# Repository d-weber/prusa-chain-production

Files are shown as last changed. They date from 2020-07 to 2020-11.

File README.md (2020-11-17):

# Prusa i3 MK3 Chain Production add-on
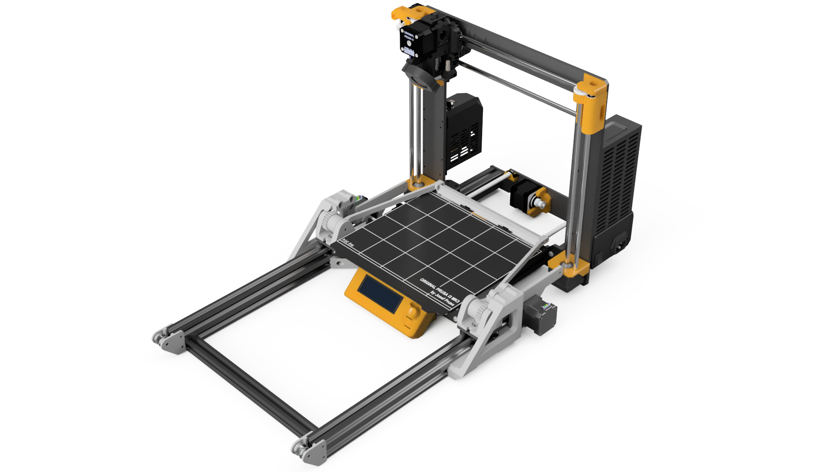
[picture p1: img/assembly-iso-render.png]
assembly iso render [assembly iso render

Add chain production capability to your Prusa i3

# How it works
- The arduino controls the steppers & fans
- The printer is controlled via octopi
- A [script](octoprint-plugin/main.py) on the octopi monitors the octoprint status and controls the arduino via usb-serial to start cooling and trigger the ejection

# Demo video
YT (https://www.youtube.com/watch?v=xZeJeUdq0wY)

# Assembly Bill of materials
Most of the parts can be ordered on Aliexpress at a small cost, for a total of approx $100

Description | Count | Français | English
------------ | ------------- | ------------- | -------------
Nema 17 stepper | 2 | [AliExpress](https://fr.aliexpress.com/item/32572890101.html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,searchweb201602_,searchweb201603_) | [AliExpress](https://www.aliexpress.com/item/32572890101.html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,searchweb201602_,searchweb201603_)
350mm 2040 V-SLOT Aluminium profile | 2 | [AliExpress](https://fr.aliexpress.com/item/32920516912.html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,searchweb201602_,searchweb201603_) | [AliExpress](https://www.aliexpress.com/item/32920516912.html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,searchweb201602_,searchweb201603_)
300mm 2020 V-SLOT Aluminium profile | 1 | [AliExpress](https://fr.aliexpress.com/item/32998701000.html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,searchweb201602_,searchweb201603_) | [AliExpress](https://www.aliexpress.com/item/32998701000.html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,searchweb201602_,searchweb201603_)
Mini V-SLOT gantry | 2 | [AliExpress](https://fr.aliexpress.com/item/32984815098.html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,searchweb201602_,searchweb201603_) | [AliExpress](https://www.aliexpress.com/item/32984815098.html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,searchweb201602_,searchweb201603_)
Angle bracket for 2020 | 2 | [AliExpress](https://fr.aliexpress.com/item/4001050647146.html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,searchweb201602_,searchweb201603_) | [AliExpress](https://www.aliexpress.com/item/4001050647146.html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,searchweb201602_,searchweb201603_)
20T 6MM GT2 Idler pulley | 2 | [AliExpress](https://fr.aliexpress.com/item/32822906447.html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,searchweb201602_,searchweb201603_) | [AliExpress](https://www.aliexpress.com/item/32822906447.html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,searchweb201602_,searchweb201603_)
20T 6MM GT2 Motor pulley | 2 | [AliExpress](https://fr.aliexpress.com/item/4000640547601.html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,searchweb201602_,searchweb201603_) | [AliExpress](https://www.aliexpress.com/item/4000640547601.html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,searchweb201602_,searchweb201603_)
1M 6MM GT2 Belt | 2 | [AliExpress](https://fr.aliexpress.com/item/32853559638.html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,searchweb201602_,searchweb201603_) | [AliExpress](https://www.aliexpress.com/item/32853559638.html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,searchweb201602_,searchweb201603_)
120MM 12V FAN | 2 | [AliExpress](https://fr.aliexpress.com/item/33000978834.html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,searchweb201602_,searchweb201603_) | [AliExpress](https://www.aliexpress.com/item/33000978834.html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,searchweb201602_,searchweb201603_)
TMC2130 SPI StepStick | 2 | [AliExpress](https://fr.aliexpress.com/item/32970150483.html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,searchweb201602_,searchweb201603_) | [AliExpress](https://www.aliexpress.com/item/32970150483.html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,searchweb201602_,searchweb201603_)
Arduino pro micro clone | 2 | [AliExpress](https://fr.aliexpress.com/item/32902569443.html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,searchweb201602_,searchweb201603_) | [AliExpress](https://www.aliexpress.com/item/32902569443.html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,searchweb201602_,searchweb201603_)
M4x10 HEX Screw | 50 | [AliExpress](https://fr.aliexpress.com/item/10000150053486.html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,searchweb201602_,searchweb201603_) | [AliExpress](https://www.aliexpress.com/item/10000150053486.html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,searchweb201602_,searchweb201603_)
M5x30 HEX Screw | 2 | [AliExpress](https://fr.aliexpress.com/item/10000150053486.html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,searchweb201602_,searchweb201603_) | [AliExpress](https://www.aliexpress.com/item/10000150053486.html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,searchweb201602_,searchweb201603_)
M5x50 HEX Screw | 2 | [AliExpress](https://fr.aliexpress.com/item/10000150053486.html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,searchweb201602_,searchweb201603_) | [AliExpress](https://www.aliexpress.com/item/10000150053486.html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,searchweb201602_,searchweb201603_)
M4x30 HEX Screw | 4 | [AliExpress](https://fr.aliexpress.com/item/10000150053486.html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,searchweb201602_,searchweb201603_) | [AliExpress](https://www.aliexpress.com/item/10000150053486.html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,searchweb201602_,searchweb201603_)
M4 NyLock Nut | 4 | [AliExpress](https://fr.aliexpress.com/item/32988995881.html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,searchweb201602_,searchweb201603_) | [AliExpress](https://www.aliexpress.com/item/32988995881.html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,searchweb201602_,searchweb201603_)
M4 2020 Nut | 50 | [AliExpress](https://fr.aliexpress.com/item/33043957747.html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,searchweb201602_,searchweb201603_) | [AliExpress](https://www.aliexpress.com/item/33043957747.html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,searchweb201602_,searchweb201603_)
M4 3030 Nut | 4 | [AliExpress](https://fr.aliexpress.com/item/33043957747.html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,searchweb201602_,searchweb201603_) | [AliExpress](https://www.aliexpress.com/item/33043957747.html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,searchweb201602_,searchweb201603_)

# Ejector PCB
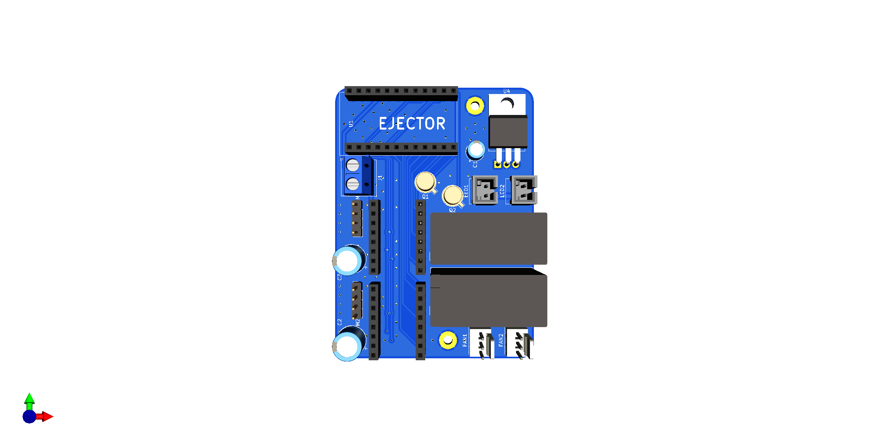
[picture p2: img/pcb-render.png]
assembly iso render [assembly iso render

Can be ordered through jlcpcb or any similar service

# Electronics Bill of materials
Description | Count | Français | English
------------ | ------------- | -------------
TMC2130 SPI StepStick | 2 | [AliExpress](https://fr.aliexpress.com/item/32970150483.html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,searchweb201602_,searchweb201603_) | [AliExpress](https://www.aliexpress.com/item/32970150483.html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,searchweb201602_,searchweb201603_)
Arduino pro micro clone | 2 | [AliExpress](https://fr.aliexpress.com/item/32902569443.html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,searchweb201602_,searchweb201603_) | [AliExpress](https://www.aliexpress.com/item/32902569443.html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,searchweb201602_,searchweb201603_)

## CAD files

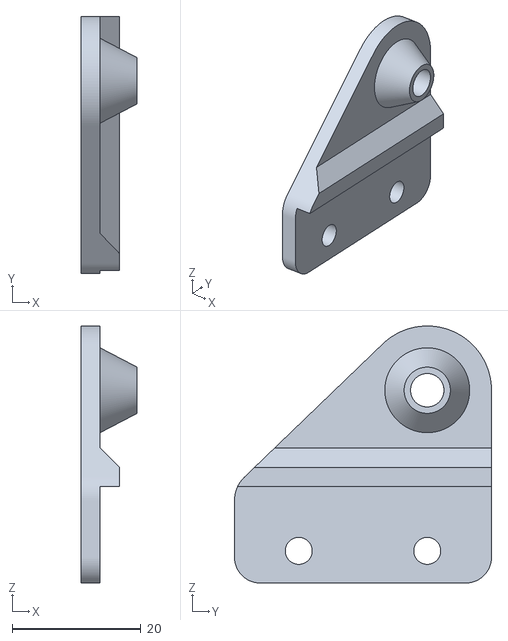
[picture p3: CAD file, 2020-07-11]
ejector-parts/stl/pulley_left.stl
8.75 x 40.0 x 40.0

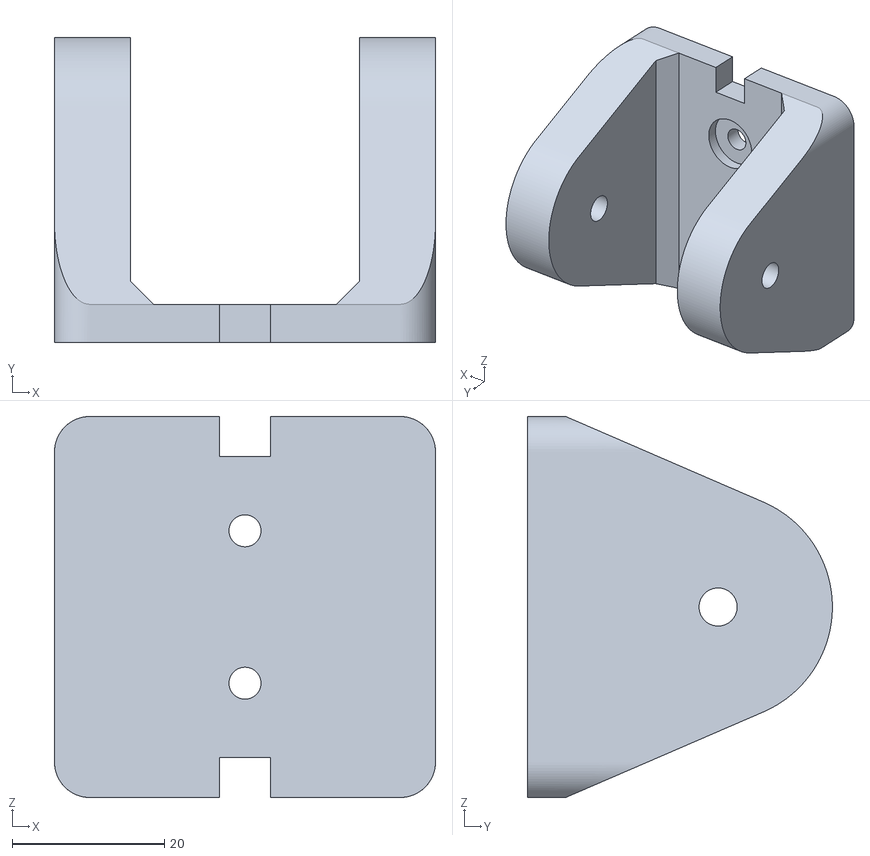
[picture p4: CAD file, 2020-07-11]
ejector-parts/stl/gear_support.stl
50.0 x 40.0 x 50.0

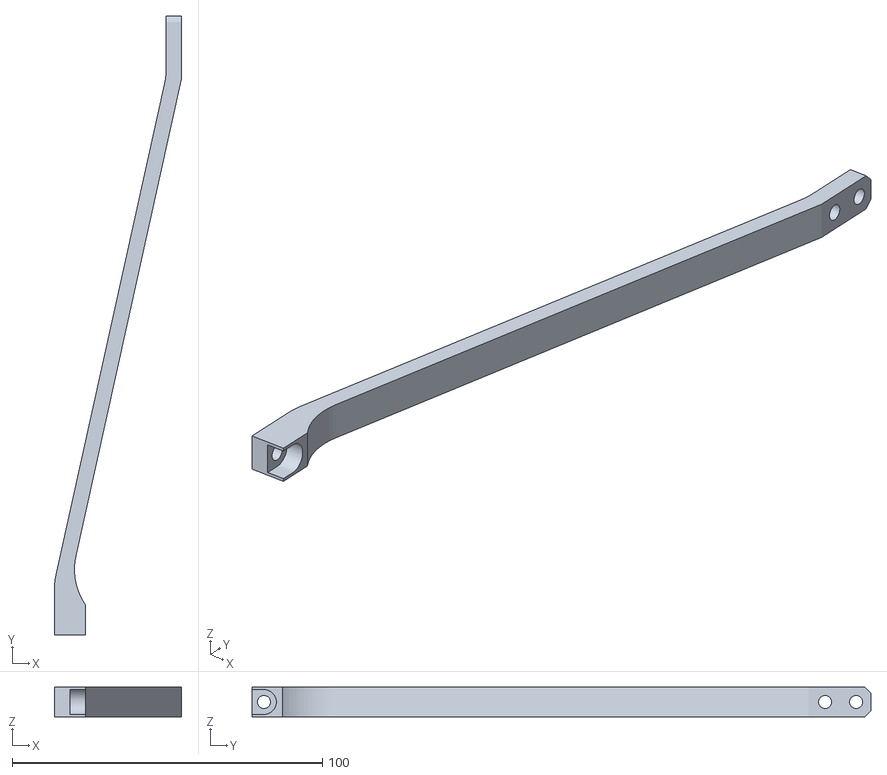
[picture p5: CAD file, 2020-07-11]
ejector-parts/stl/scrapper_arm_left.stl
41.0 x 199.6 x 9.60

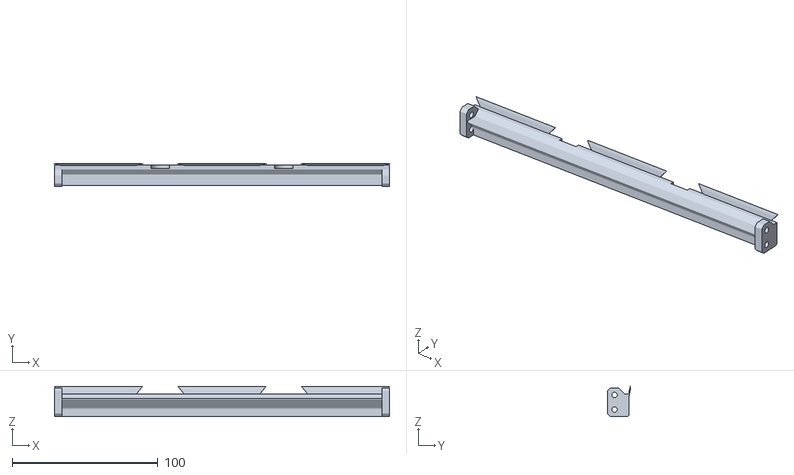
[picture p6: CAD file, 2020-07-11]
ejector-parts/stl/scrapper.stl
230.1 x 15.7 x 20.6

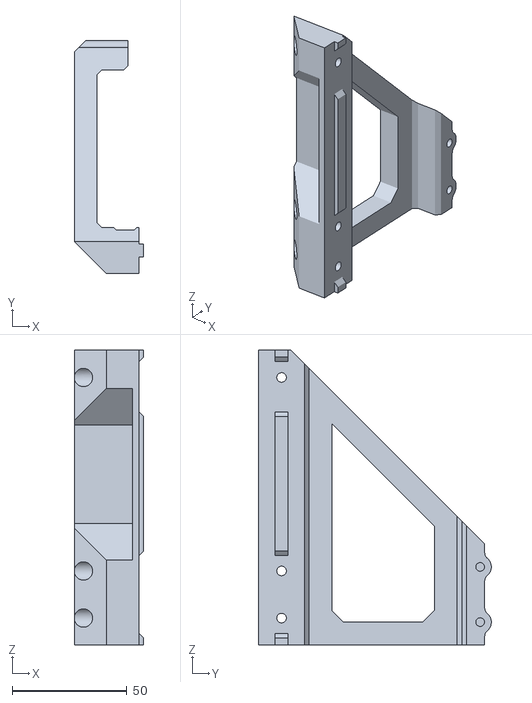
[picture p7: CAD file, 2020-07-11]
ejector-parts/stl/rack_support_left.stl
30.3 x 101.6 x 128.8

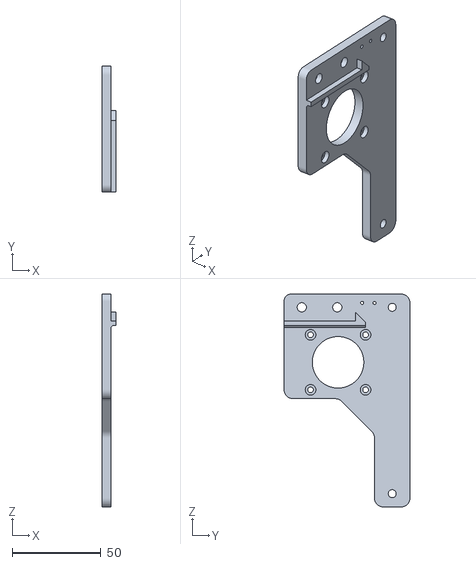
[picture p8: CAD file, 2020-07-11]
ejector-parts/stl/motor_mount_left.stl
8.00 x 70.9 x 120.0

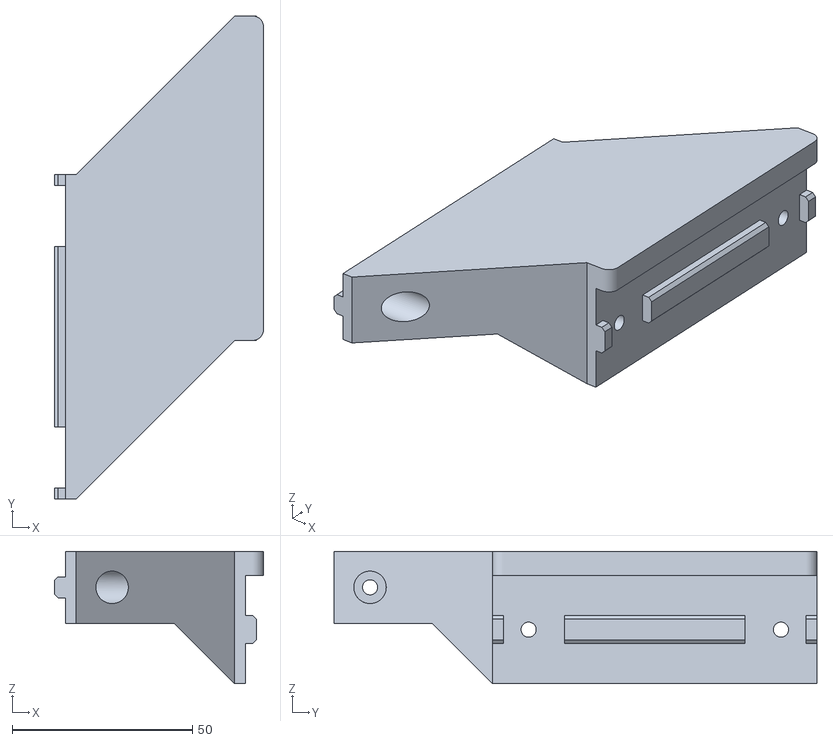
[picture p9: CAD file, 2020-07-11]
ejector-parts/stl/link_right.stl
58.0 x 134.0 x 36.8

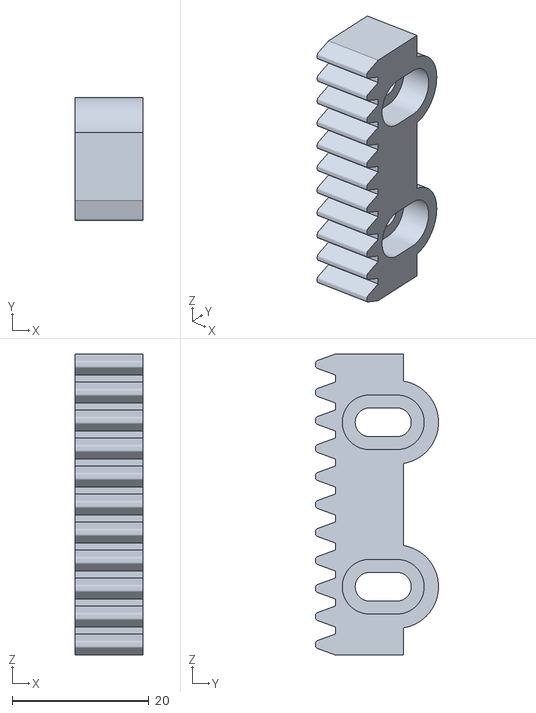
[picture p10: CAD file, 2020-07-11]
ejector-parts/stl/gear_rack.stl
10.00 x 18.0 x 44.1

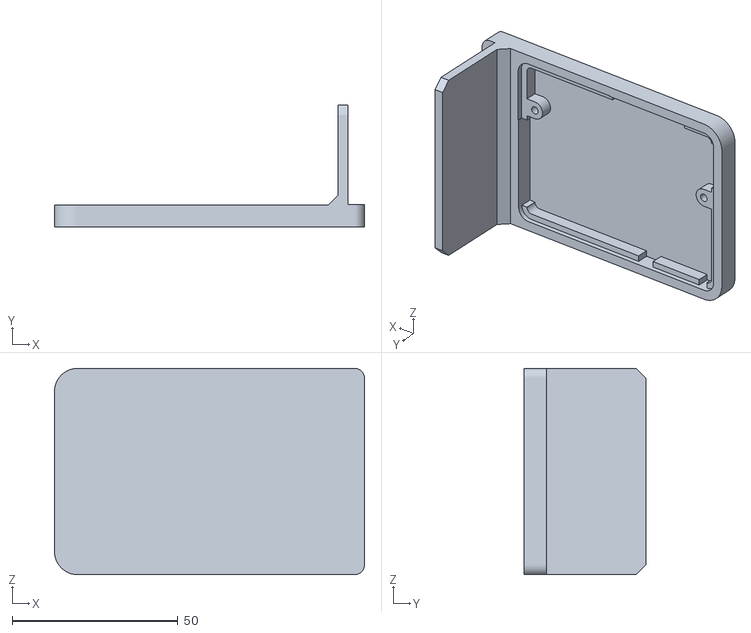
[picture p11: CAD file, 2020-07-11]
ejector-parts/stl/pcb_holder.stl
93.5 x 36.7 x 62.3

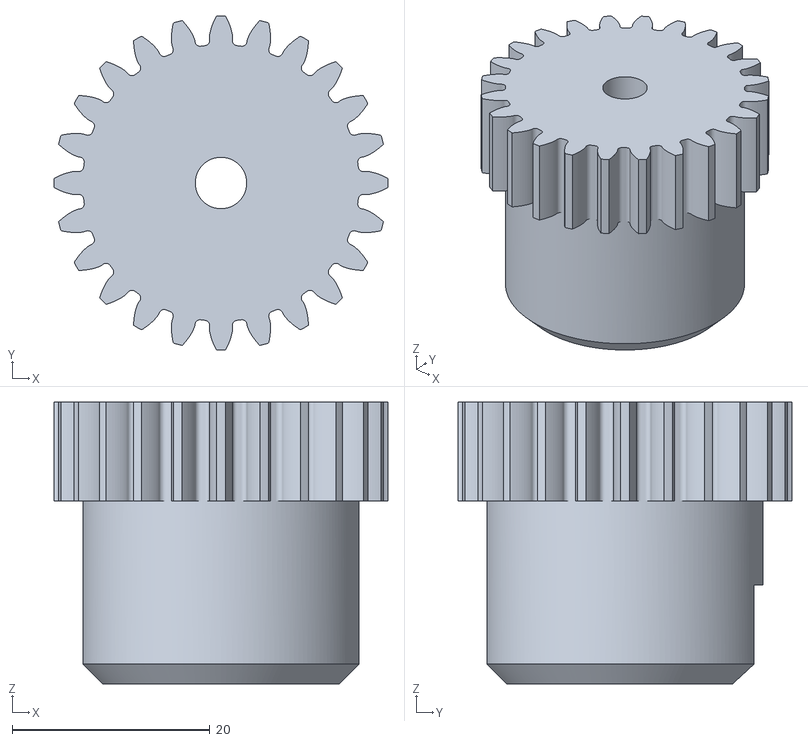
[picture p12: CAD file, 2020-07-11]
ejector-parts/stl/gear.stl
33.8 x 33.8 x 28.5

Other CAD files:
ejector-parts/stl/rack_support_right.stl
ejector-parts/stl/link_left.stl
ejector-parts/stl/scrapper_arm_right.stl
ejector-parts/stl/motor_mount_right.stl
ejector-parts/stl/pulley_right.stl

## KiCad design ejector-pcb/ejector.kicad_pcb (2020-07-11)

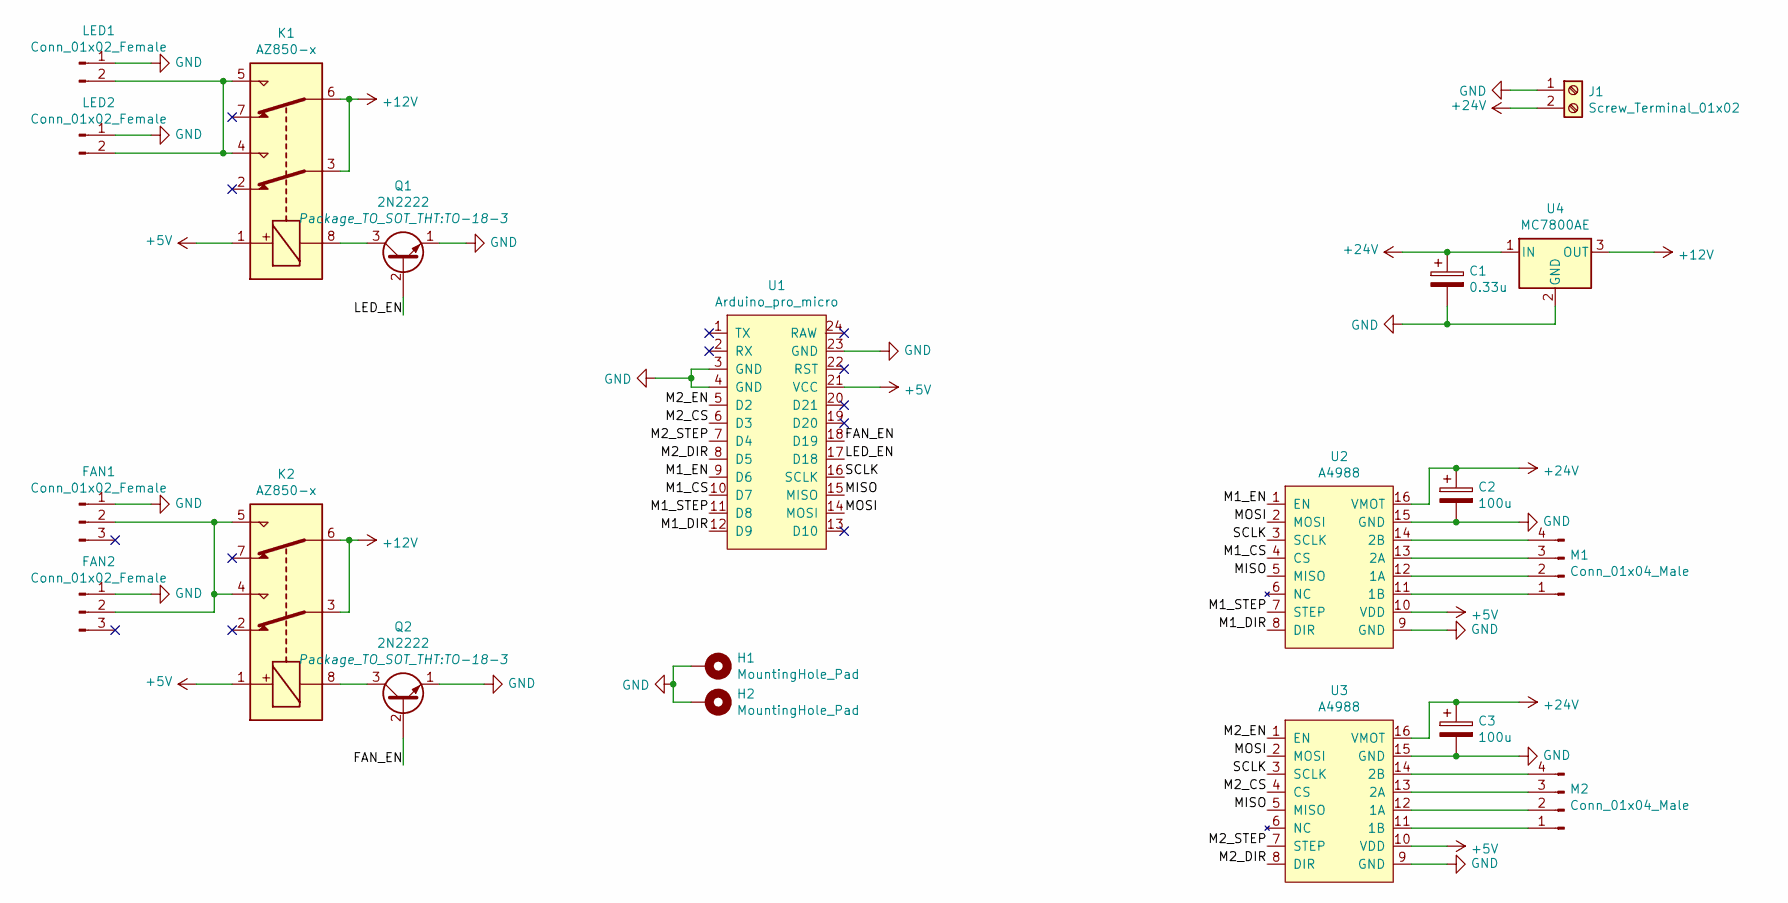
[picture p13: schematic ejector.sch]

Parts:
C1: 0.33u; CP_Radial_D5.0mm_P2.00mm
C2, C3: 100u; CP_Radial_D8.0mm_P3.50mm
FAN1, FAN2: Conn_01x02_Female; Molex_KK-254_AE-6410-03A_1x03_P2.54mm_Vertical
H1, H2: MountingHole_Pad; MountingHole_2.5mm_Pad
J1: Screw_Terminal_01x02; TerminalBlock_Phoenix_MKDS-1,5-2-5.08_1x02_P5.08mm_Horizont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
K1, K2: AZ850-x; Relay_DPDT_Panasonic_JW2
LED1, LED2: Conn_01x02_Female; Molex_SL_171971-0002_1x02_P2.54mm_Vertical
M1, M2: Conn_01x04_Male; PinHeader_1x04_P2.54mm_Vertical
Q1, Q2: 2N2222; TO-18-3
U1: Arduino_pro_micro; ARDUINOPROMICRO
U2, U3: A4988
U4: MC7800AE; TO-220-3_Horizontal_TabDown

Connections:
+5V: K1.1, K2.1, U1.21 (VCC), U2.10 (VDD), U3.10 (VDD)
+12V: K1.3, K1.6, K2.3, K2.6, U4.3 (OUT)
+24V: C1.1, C2.1, C3.1, J1.2, U2.16 (VMOT), U3.16 (VMOT), U4.1 (IN)
/FAN_EN: Q2.2 (B), U1.18 (D19)
/LED_EN: Q1.2 (B), U1.17 (D18)
/M1_CS: U1.10 (D7), U2.4 (CS)
/M1_DIR: U1.12 (D9), U2.8 (DIR)
/M1_EN: U1.9 (D6), U2.1 (EN)
/M1_STEP: U1.11 (D8), U2.7 (STEP)
/M2_CS: U1.6 (D3), U3.4 (CS)
/M2_DIR: U1.8 (D5), U3.8 (DIR)
/M2_EN: U1.5 (D2), U3.1 (EN)
/M2_STEP: U1.7 (D4), U3.7 (STEP)
/MISO: U1.15 (MISO), U2.5 (MISO), U3.5 (MISO)
/MOSI: U1.14 (MOSI), U2.2 (MOSI), U3.2 (MOSI)
/SCLK: U1.16 (SCLK), U2.3 (SCLK), U3.3 (SCLK)
GND: C1.2, C2.2, C3.2, FAN1.1, FAN2.1, H1.1, H2.1, J1.1, LED1.1, LED2.1, Q1.1 (E), Q2.1 (E), U1.3 (GND), U1.4 (GND), U1.23 (GND), U2.9 (GND), U2.15 (GND), U3.9 (GND), U3.15 (GND), U4.2 (GND)
unnamed: FAN1.2, FAN2.2, K2.4, K2.5
unnamed: K1.4, K1.5, LED1.2, LED2.2
unnamed: K1.8, Q1.3 (C)
unnamed: K2.8, Q2.3 (C)
unnamed: M1.1, U2.11 (1B)
unnamed: M1.2, U2.12 (1A)
unnamed: M1.3, U2.13 (2A)
unnamed: M1.4, U2.14 (2B)
unnamed: M2.1, U3.11 (1B)
unnamed: M2.2, U3.12 (1A)
unnamed: M2.3, U3.13 (2A)
unnamed: M2.4, U3.14 (2B)

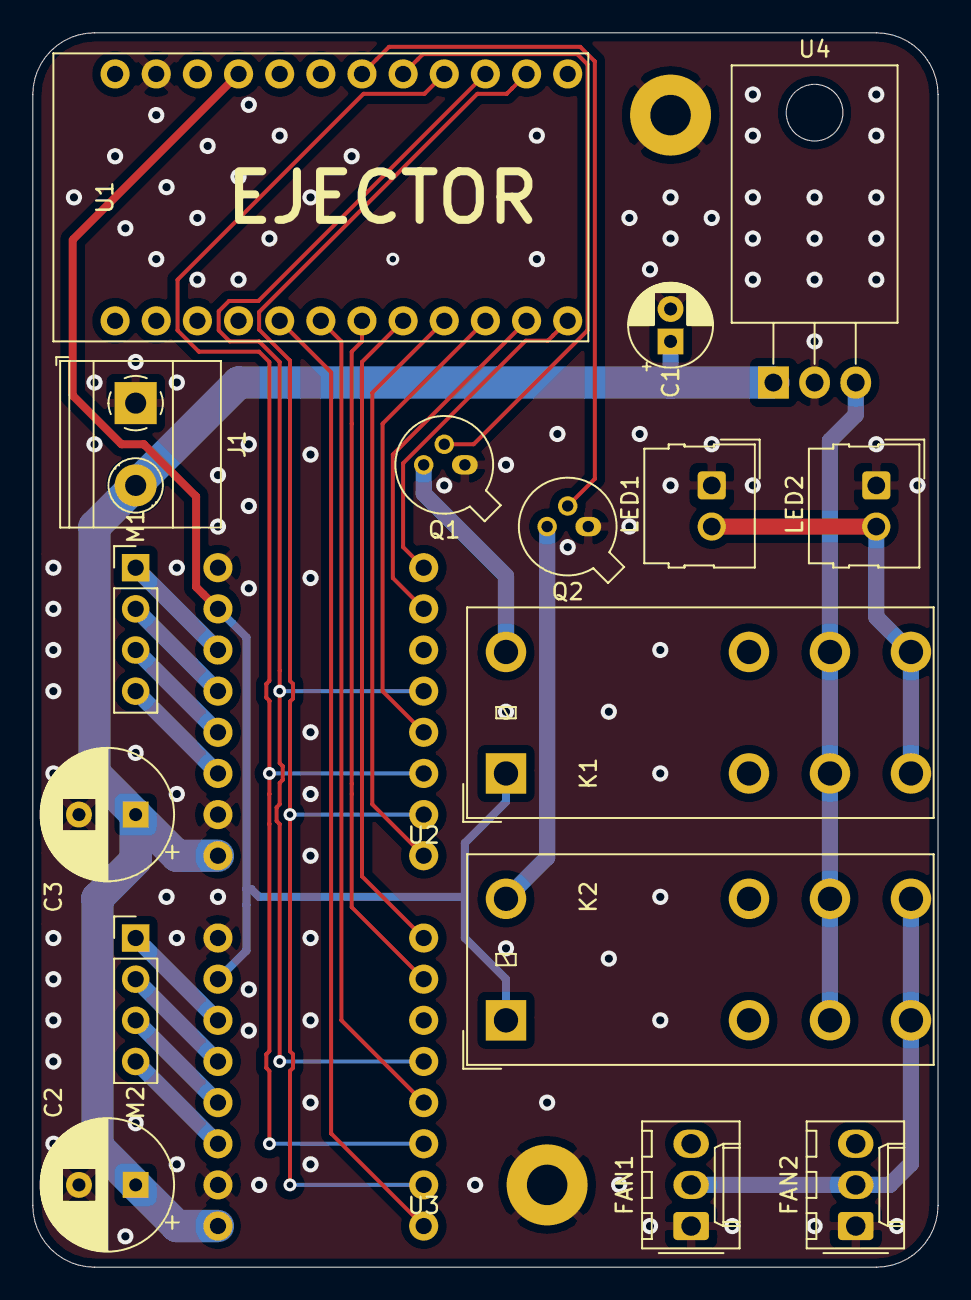
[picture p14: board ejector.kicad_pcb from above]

Board: 2 copper layers, 55.9 x 76.2 mm, 20 parts (0 on the bottom side), 29 nets.

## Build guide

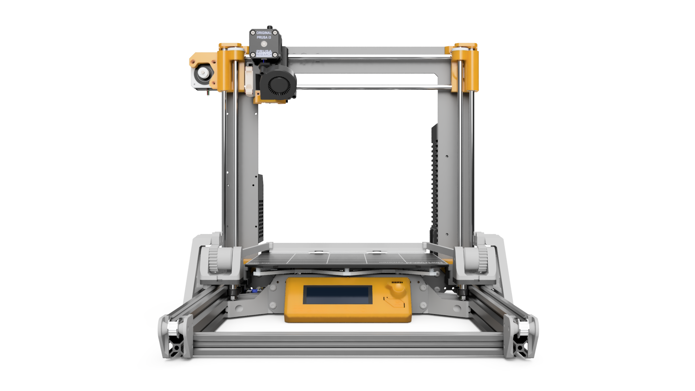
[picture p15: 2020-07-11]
img/assembly-front-render.png

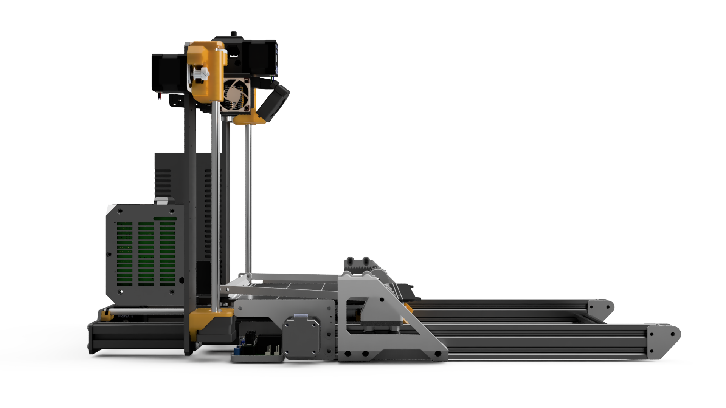
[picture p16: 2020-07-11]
img/assembly-left-render.png

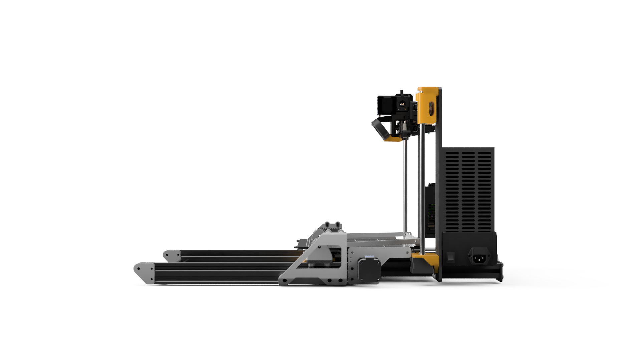
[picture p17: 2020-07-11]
img/assembly-right-render.png

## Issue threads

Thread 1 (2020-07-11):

Needs an octoprint plugin

d-weber, 2020-07-11:
We should be able to control the ejector via octoprint & also queue prints.

d-weber, 2020-07-11:
The plugin may allow to:
- Select & Save the arduino port (same as for the printer)
- Manually trigger Ejector procedure
- Manually trigger FAN OFF/ON
- Manually trigger LED OFF/ON
- Set the cooling time after a print is finished (15min for me)
- Queue gcodes & number of prints per gcode

Arduino baudrate : 9600
All commands must end with `\n`

Arduino commands:
Description | Command | Response
----- | ----- | -----
Connection test | PING | PONG
Homing | HOME | START & END
Extend ejector | END | START & END
Ejection procedure) | EJECT | START & END
Turn on fans | FAN ON | DONE
Turn off fans | FAN OFF | DONE
Turn on leds | LED ON | DONE
Turn on leds | LED OFF | DONE

mmiscool, 2020-07-11:
Hello,
I am with Autodrop3d and would love to talk with you about the possibility of connecting to our cloud print platform that has queing and was specifically designed for printers with automatic part ejection. We have a gcode sender client that runs on a raspberry pi written in python. I think it would be a matter of a few hours to make a plug-in that handles your unique ejector and I would be happy to hop on a call to make that happen.

A little background on Autodrop3d. It has queing, routing to machine based on print size, location and material. It also supports monitization in shared private or public environments. The platform also included built in browser based parametric modeling allowing for a completely web based 3d printer workflow.

If you are interested we can set up a Google Hangouts meet and make it happen.

d-weber, 2020-07-21:
Thanks @mmiscool , i think you have all the data in this repo to make a plugin for you interface, you can simply plug the arduino on your raspberry ;).

However we're discussing about an octoprint plugin here :)

Faceless3D, 2020-11-21:
Hi,

i´m having troubles getting the octoprint plugin to work. Do i have to modify the main.py and insert the API and IP Adress of the Pi? Do i use the global API or a application API Key ? Is port 80 always correct? Under /dev i can see ttyACM0 but not ttyACM1 which one is correct? I´m using a Raspberry Pi Zero. Do i "install" the Plugin via the Plugin Manager in Octoprint?

Sorry for so many question. It´s the last step of getting this system to work.

Thank you

Faceless3D, 2020-11-25:
Hi,

how do you queue or loop printjobs right now? Is there an elegant way of doing it?
I use the plugin "continuous print" with a wait time between jobs (G4 Pxxx). The wait time is the cooling time + ejection duration. While waiting between jobs the printer status is "finishing", i had to replace "operational" with "finishing"  in the plugin.

So this method of bed cleaing works perfect with PETG and the textured PEI bed. Now i have to build 10 more for the whole farm.

Thank you

Marwitch, 2021-06-08:
Hello,
the octoprint plugin does not work for me.
Is it possible to make an update please?
-----------------------------------------------------------------------
Incompatible to OctoPrint or the underlying Python environment
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

Marwitch, 2021-06-08:
Hello!
so what about the plugin?

Marwitch, 2021-06-09:
Hello @d-weber,
unfortunately the plugin is no longer functional.
Please update :)

modtoy95, 2021-09-14:
how can i get this working on octo print?

Marwitch, 2021-09-14:
Hi, I made my own motor control and my own code for arduino :) I use the "continuous print" plugin in octoprint. Everything works the same just I don't have communication between the printer and raspberry ..

modtoy95, 2021-09-15:
would you be willing to share how you did i?

modtoy95, 2021-09-15:
it?

bastian123321, 2022-06-02:
It seems that the plugin isnt working anymore on new Octoprint versions, was the plugin written in python 2 or 3?

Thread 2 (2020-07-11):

Update the arduino code for TMC2130 support

d-weber, 2020-07-11:
The arduino code is actually made for A4988 drivers & 4 microswitch endstops

It should use TMC2130 stallguard function to detect endstops & detect ejection fails to retry

Faceless3D, 2020-11-07:
Hi,

thank you for this great project! I just finished the PCB and want to test the system. Do you know when the code for the TMC2130 Stepper is available? Unfortunetly i can´t code :(

Thank you

Faceless3D, 2020-11-07:
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

d-weber, 2020-11-17:
Great ! i'll update the code tonight

d-weber, 2020-11-17:
Done, you mayd need to tune STALL_VALUE @Faceless3D

Faceless3D, 2020-11-21:
Thank you!

STALL_VALUE 9 works good for me. I also increased the acceleration a bit.

d-weber, 2020-12-18:
Implemented in #9

bnykolass, 2022-06-03:
Please, where should I put the script in octoprint?
It doesn't work for me as a plugin.
Well thank you

Closed 2020-12-18.

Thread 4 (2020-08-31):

Pulley bores missing

tim-lukacik, 2020-08-31:
I believe the bill of materials is missing one specification for
20T 6MM GT2 Idler pulley
20T 6MM GT2 Motor pulley

I assume "B5" idler, "inner hole 5mm" motor as these are riding on the m5 screws?

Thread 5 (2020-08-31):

PCB ordering guide

tim-lukacik, 2020-08-31:
When trying to order the PCB I am able to upload the gerber.zip file successfully but how do I provide the SMT components for assembly? JLCPCB seems to be looking for BOM or CPL files. Sorry if I am missing something I have not ordered custom PCBs before.

I can make a PR with a guide for others once I understand the whole process.

Baelt, 2021-02-02:
hello there
I would also be very interested in how to buy/order the PCB...
Greetings Ulrich

modtoy95, 2021-08-24:
Did you figure out how to add or generate a BOM file?

Marwitch, 2021-09-14:
I had the PCB made and used all the components, unfortunately after measuring I found out that the PCB is badly made and I threw it away! I made my own code for arduino and I control it via the endstop switch :D

modtoy95, 2021-09-14:
Thats exactly what I was thinking of doing. With an end stop switch. I even looked around on fiver to see if some on could code something similar. Would it be to much to ask if you are willing to share or sell your idea to me? I've been trying to automated my printers for a while now. I even bought quinley automation, but I'm not a fan of the print head pushing the parts out. 

Sent from Yahoo Mail on Android

  On Tue, Sep 14, 2021 at 12:35 AM, ***@***.***> wrote:

I had the PCB made and used all the components, unfortunately after measuring I found out that the PCB is badly made and I threw it away! I made my own code for arduino and I control it via the endstop switch :D

—
You are receiving this because you commented.
Reply to this email directly, view it on GitHub, or unsubscribe.
Triage notifications on the go with GitHub Mobile for iOS or Android.

modtoy95, 2021-09-15:
I hired some one on fiver to rewrite the code to trigger with a switch, but nothing happens idk what's wrong. 

Sent from Yahoo Mail on Android

  On Tue, Sep 14, 2021 at 2:47 AM, Luis ***@***.***> wrote:   Thats exactly what I was thinking of doing. With an end stop switch. I even looked around on fiver to see if some on could code something similar. Would it be to much to ask if you are willing to share or sell your idea to me? I've been trying to automated my printers for a while now. I even bought quinley automation, but I'm not a fan of the print head pushing the parts out. 

Sent from Yahoo Mail on Android

  On Tue, Sep 14, 2021 at 12:35 AM, ***@***.***> wrote:

I had the PCB made and used all the components, unfortunately after measuring I found out that the PCB is badly made and I threw it away! I made my own code for arduino and I control it via the endstop switch :D

—
You are receiving this because you commented.
Reply to this email directly, view it on GitHub, or unsubscribe.
Triage notifications on the go with GitHub Mobile for iOS or Android.

KilianWS, 2021-11-16:
hello there
has someone found a way to create the BOM and CPL file for JLCPCB?
@tim-lukacik or did you find another way to order it?

tyneff, 2022-12-11:
Hi,

Also having trouble getting the PCB made with all components. Has anyone been able to do so successfully? Would happily purchase a built PCB

ant0nyk1ng, 2023-11-29:
> I hired some one on fiver to rewrite the code to trigger with a switch, but nothing happens idk what's wrong.  Sent from Yahoo Mail on Android On Tue, Sep 14, 2021 at 2:47 AM, Luis ***@***.***> wrote: Thats exactly what I was thinking of doing. With an end stop switch. I even looked around on fiver to see if some on could code something similar. Would it be to much to ask if you are willing to share or sell your idea to me? I've been trying to automated my printers for a while now. I even bought quinley automation, but I'm not a fan of the print head pushing the parts out.  Sent from Yahoo Mail on Android On Tue, Sep 14, 2021 at 12:35 AM, ***@***.***> wrote: I had the PCB made and used all the components, unfortunately after measuring I found out that the PCB is badly made and I threw it away! I made my own code for arduino and I control it via the endstop switch :D — You are receiving this because you commented. Reply to this email directly, view it on GitHub, or unsubscribe. Triage notifications on the go with GitHub Mobile for iOS or Android.

Did you get this to work? can I chat to you about what you did?

ant0nyk1ng, 2023-11-29:
> I had the PCB made and used all the components, unfortunately after measuring I found out that the PCB is badly made and I threw it away! I made my own code for arduino and I control it via the endstop switch :D

I see you have a fork but there is no information on the arduino code?

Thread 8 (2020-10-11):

Can this system work with a smooth pei sheet?

DoWhileGeek, 2020-10-11:
I can see how a textured bed works really well for this system, as most parts will pop themselves loose, especially given the cooling routine. But what about smooth pei? Most of my products need to be printed on a smooth sheet, and I was wondering if you've done any testing with it?

Marwitch, 2021-09-14:
Hi, I also print on a smooth surface and it's no problem. You just have to be careful to adjust the guide knife on the pad! It is better to adjust the whole part and not put sharp edges there, as this could damage the pad!

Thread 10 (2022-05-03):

How does this system communicate with the 3D printer?

JimmyRam, 2022-05-03:
Does this system get connected directly to a raspberry pi and get controlled through octo print or does it get connected to the main board some how. I'm a bit confused on how to wire everything together? I'm still pretty new to electronics so I might just be missing something obvious.

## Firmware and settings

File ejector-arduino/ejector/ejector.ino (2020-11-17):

#include <TMCStepper.h>
#include <AccelStepper.h>
#define R_SENSE 0.11f
using namespace TMC2130_n;

// Serial commands
#define CMD_UNKNOWN 0
#define CMD_PING    1
#define CMD_HOME    2
#define CMD_END     3
#define CMD_EJECT   4
#define CMD_FAN_ON  5
#define CMD_FAN_OFF 6
#define CMD_LED_ON  7
#define CMD_LED_OFF 8
#define CMD_MOVE_FRONT 9
#define CMD_MOVE_REAR 10

// Motor 1
#define PIN_M1_ENABLE 6
#define PIN_M1_CS 7
#define PIN_M1_STEP 8
#define PIN_M1_DIR 9
TMC2130Stepper driverM1(PIN_M1_CS, R_SENSE);
AccelStepper stepperM1 = AccelStepper(AccelStepper::DRIVER, PIN_M1_STEP, PIN_M1_DIR);

// Motor 2
#define PIN_M2_ENABLE 2
#define PIN_M2_CS 3
#define PIN_M2_STEP 4
#define PIN_M2_DIR 5
TMC2130Stepper driverM2(PIN_M2_CS, R_SENSE);
AccelStepper stepperM2 = AccelStepper(AccelStepper::DRIVER, PIN_M2_STEP, PIN_M2_DIR);

// Other pins
#define PIN_LED 18
#define PIN_FAN 19

// Config
#define MICROSTEP 4
#define MAX_MOVING_TIME 10 // s
#define DEBUG false 
#define STEPS_PER_MM 5
#define STALL_VALUE 6
#define MAX_STALL 100

int maxPos = 280;
long mm2Step(long distance) {
  return  distance * STEPS_PER_MM * MICROSTEP;
}

long step2mm(long step) {
  return step / STEPS_PER_MM / MICROSTEP;
}

void setup() {
  Serial.begin(115200);

  // Fan & leds relays
  pinMode(PIN_LED, OUTPUT);
  pinMode(PIN_FAN, OUTPUT);
  pinMode(PIN_M1_CS, OUTPUT);
  pinMode(PIN_M2_CS, OUTPUT);

  while (!Serial) {
    ; // wait for serial port to connect. Needed for native USB
  }

  // Test relays
  digitalWrite(PIN_FAN, HIGH); 
  delay(1000);
  digitalWrite(PIN_FAN, LOW); 
  delay(500);
  digitalWrite(PIN_LED, HIGH); 
  delay(1000);
  digitalWrite(PIN_LED, LOW);

  // Enable SPI
  SPI.begin();
  pinMode(MISO, INPUT_PULLUP);

  // Init M1
  driverM1.begin();
  driverM1.rms_current(1000);
  driverM1.toff(4);
  driverM1.blank_time(24);
  driverM1.microsteps(MICROSTEP);
  driverM1.TCOOLTHRS(0xFFFFF); // 20bit max
  driverM1.THIGH(0);
  driverM1.semin(5);
  driverM1.semax(2);
  driverM1.sedn(0b01);
  driverM1.sgt(STALL_VALUE);
  driverM1.switchCSpin(LOW);
  stepperM1.setMaxSpeed(100 * MICROSTEP);
  stepperM1.setAcceleration(1000 * MICROSTEP);
  stepperM1.setEnablePin(PIN_M1_ENABLE);
  stepperM1.setPinsInverted(false, false, true);
  stepperM1.disableOutputs();

  // Init M2
  driverM2.begin();
  driverM2.rms_current(1000);
  driverM2.toff(4);
  driverM2.blank_time(24);
  driverM2.microsteps(MICROSTEP);
  driverM2.TCOOLTHRS(0xFFFFF); // 20bit max
  driverM2.THIGH(0);
  driverM2.semin(5);
  driverM2.semax(2);
  driverM2.sedn(0b01);
  driverM2.sgt(STALL_VALUE);
  driverM2.switchCSpin(LOW);
  stepperM2.setMaxSpeed(100 * MICROSTEP);
  stepperM2.setAcceleration(1000 * MICROSTEP);
  stepperM2.setEnablePin(PIN_M2_ENABLE);
  stepperM2.setPinsInverted(false, false, true);
  stepperM2.disableOutputs();
}

int parseStringCommand(String stringCommand) {
    if (stringCommand.equals("PING")) {
      return CMD_PING;
    } else if (stringCommand.equals("MOVE FRONT")) {
      return CMD_MOVE_FRONT;
    } else if (stringCommand.equals("MOVE REAR")) {
      return CMD_MOVE_REAR;
    } else if (stringCommand.equals("HOME")) {
      return CMD_HOME;
    } else if (stringCommand.equals("END")) {
      return CMD_END;
    } else if (stringCommand.equals("EJECT")) {
      return CMD_EJECT;
    } else if (stringCommand.equals("FAN ON")) {
      return CMD_FAN_ON;
    } else if (stringCommand.equals("FAN OFF")) {
      return CMD_FAN_OFF;
    } else if (stringCommand.equals("LED ON")) {
      return CMD_LED_ON;
    } else if (stringCommand.equals("LED OFF")) {
      return CMD_LED_OFF;
    } else {
      return CMD_UNKNOWN  ;
    }
}

int getM1StallValue() {
  DRV_STATUS_t drv_status{0};
  drv_status.sr = driverM1.DRV_STATUS();
  return drv_status.sg_result;
}

int getM2StallValue() {
  DRV_STATUS_t drv_status{0};
  drv_status.sr = driverM2.DRV_STATUS();
  return drv_status.sg_result;
}

long moveTo(long distance, long speed, bool sync = true) {
  stepperM1.setMaxSpeed(speed * MICROSTEP);
  stepperM2.setMaxSpeed(speed * MICROSTEP);
  stepperM1.moveTo(mm2Step(distance));
  stepperM2.moveTo(mm2Step(distance));
  uint32_t startTime = millis();
  uint32_t lastTime = millis();
  uint32_t lastStallCheck = millis();
  while(true) {
    stepperM1.run();
    stepperM2.run();

    if ((millis() - lastStallCheck) > 10) {
      lastStallCheck = millis();
      int M1StallValue = getM1StallValue();
      int M2StallValue = getM2StallValue();

      if ((millis() - startTime) > 100 && (M1StallValue < MAX_STALL || M2StallValue < MAX_STALL)){
        if (M1StallValue < MAX_STALL) {
          if (DEBUG) Serial.print("Stalled M1: ");
          if (DEBUG) Serial.println(M1StallValue, DEC);
          stepperM1.move(0);
          stepperM1.setSpeed(0);
        }
        if (M2StallValue < MAX_STALL) {
          if (DEBUG) Serial.print("Stalled M2: ");
          if (DEBUG) Serial.println(M2StallValue, DEC);
          stepperM2.move(0);
          stepperM2.setSpeed(0);
        }
        if (sync) {
          stepperM1.move(0);
          stepperM2.move(0);
          stepperM1.setSpeed(0);
          stepperM2.setSpeed(0);
        }
        break;
      }
    }

    if (!stepperM1.isRunning() && !stepperM2.isRunning()){
      break;
    }
  }

  long avgPos = (stepperM1.currentPosition() + stepperM2.currentPosition()) / 2;
  return step2mm(avgPos);
}

void eject() {
  stepperM1.enableOutputs();
  stepperM2.enableOutputs();

  // Deploy arm
  int pos = moveTo(70, 100);
  int i = 0;
  int speeds[] = {600, 500, 400, 300, 200};

  while (pos < maxPos * 0.95) {
    stepperM1.move(0);
    stepperM2.move(0);
    stepperM1.setSpeed(0);
    stepperM2.setSpeed(0);

    delay(500);
    moveTo(70, 500);
    delay(500);

    pos = moveTo(maxPos, speeds[i]);
    i++;
    if (i > 4) {
      i = 0;
    }
  }
  while (pos > 75) {
    pos  = moveTo(70, 500);
  }
  while (pos > 5) {
    pos  = moveTo(0, 100);
  }
  
  stepperM1.disableOutputs();
  stepperM2.disableOutputs();
}

void loop() {
  if (Serial.available() > 0) {
    String stringCommand = Serial.readStringUntil('\n');
    int command = parseStringCommand(stringCommand);
    switch (command) {
      case CMD_PING:
        Serial.println("PONG");
        break;
      case CMD_END:
        Serial.println("START");
        Serial.println("END");
        break;
      case CMD_EJECT:
        Serial.println("START");
        eject();
        Serial.println("END");
        break;
      case CMD_FAN_ON:
        digitalWrite(PIN_FAN, HIGH); 
        Serial.println("DONE");
        break;
      case CMD_FAN_OFF:
        digitalWrite(PIN_FAN, LOW); 
        Serial.println("DONE");
        break;
      case CMD_LED_ON:
        digitalWrite(PIN_LED, HIGH); 
        Serial.println("DONE");
        break;
      case CMD_LED_OFF:
        digitalWrite(PIN_LED, LOW); 
        Serial.println("DONE");
        break;
      default:
      case CMD_UNKNOWN:
        Serial.println("UNKNOWN COMMAND");
    }
  }
}

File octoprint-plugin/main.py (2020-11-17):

import requests
import sys
import time
import datetime
import json
import serial

# Constants
OCTOPRINT_API_KEY = ''
OCTOPRINT_HOST = 'localhost'
OCTOPRINT_PORT = '80'
EJECTOR_TTY = '/dev/ttyACM1'
EJECTION_TEMP = 30
COOLING_TIME = 900 # 15Min
AUTO_RESTART = False

# Printer status
STATUS_IDLE = 0
STATUS_PRINTING = 1
STATUS_COOLING = 2
STATUS_EJECTING = 3
STATUS_RESTARTING = 4

def log(text):
    print(datetime.datetime.now().strftime('%b %d %H:%M:%S ') + text)

log('Initalizing')

# Init
Session = requests.Session()
Session.headers.update({
    'X-Api-Key': OCTOPRINT_API_KEY,
    'Content-Type': 'application/json'
})
BaseAdress = 'http://' + OCTOPRINT_HOST + ':' + str(OCTOPRINT_PORT)
Serial = serial.Serial(EJECTOR_TTY, 9600, timeout=500) # 1s timeout

# Let time to the extrude to initialize
time.sleep(10)

# Test ejector connection
Serial.write(b"PING\n")
if Serial.readline().decode('utf-8').rstrip() == 'PONG':
    log("Ejector connected")
else:
    raise Exception('Error connecting to ejector')

# Test octoprint connection
Result = Session.get(BaseAdress + '/api/printer')
if Result.status_code != 200:
    raise Exception('Error trying to get printer connection status')
try:
    Status = json.loads(Result.content.decode('utf-8'))["state"]["flags"]["operational"]  
    if Status is True:
        log('Printer connected, starting monitoring')
    else:
        raise Exception('Error trying to get printer connection status')
except:
    raise Exception('Error trying to get printer connection status')

def getUrl(path):
    while True:
        try:
            Result = Session.get(BaseAdress + path)

            if Result.status_code != 200:
                raise Exception("Error: {code} - {content}".format(code=Result.status_code, content=Result.content.decode('utf-8')))

            return json.loads(Result.content.decode('utf-8'))
        except Exception as exc:
            log(str(exc))
            time.sleep(1)

def postUrl(path, data):
    while True:
        try:
            result = Session.post(BaseAdress + path, json=data)
            if result.status_code != 204:
                raise Exception("Error: {code} - {content}".format(code=result.status_code, content=result.content.decode('utf-8')))

            return result
        except Exception as exc:
            log(str(exc))
            time.sleep(1)

printerStatus = STATUS_IDLE
coolingStart = 0

# Desactivate everything
Serial.write(b"LED OFF\n")
Result = Serial.readline().decode('utf-8').rstrip()
if Result == 'DONE':
    log("Led off")
else:
    log('Wrong result:' + Result)
    raise Exception('Error trying to stop leds')

Serial.write(b"FAN OFF\n")
Result = Serial.readline().decode('utf-8').rstrip()
if Result == 'DONE':
    log("Fan off")
else:
    log('Wrong result:' + Result)
    raise Exception('Error trying to stop cooling')

# Loop
while True:
    # Check for octoprint status:
    Status = getUrl('/api/printer')["state"]["text"]

    if Status == 'Printing':
        if printerStatus is not STATUS_PRINTING:
            log("Printer is printing")

            Serial.write(b"FAN OFF\n")
            Result = Serial.readline().decode('utf-8').rstrip()
            if Result == 'DONE':
                log("Fan off")
            else:
                log('Wrong result:' + Result)
                raise Exception('Error trying to stop cooling')

            Serial.write(b"LED ON\n")
            Result = Serial.readline().decode('utf-8').rstrip()
            if Result == 'DONE':
                log("Led on")
            else:
                log('Wrong result:' + Result)
                raise Exception('Error trying to start leds')
            printerStatus = STATUS_PRINTING
    elif Status == 'Operational':
        # Just finished printing
        if printerStatus is STATUS_PRINTING:
            log("Print finished, cooling for " + str(COOLING_TIME/60) + "min...")
            coolingStart = time.time()
            Serial.write(b"LED OFF\n")
            Result = Serial.readline().decode('utf-8').rstrip()
            if Result == 'DONE':
                log("Led off")
            else:
                log('Wrong result:' + Result)
                raise Exception('Error trying to stop leds')
            Serial.write(b"FAN ON\n")
            Result = Serial.readline().decode('utf-8').rstrip()
            if Result == 'DONE':
                log("Cooling started")
            else:
                log('Wrong result:' + Result)
                raise Exception('Error trying to start cooling')

            # Ensure printer is in good position:
            postUrl('/api/printer/command', {'commands': ['G1 X125 Y170']})
            postUrl('/api/printer/command', {'commands': ['G1 Z210']})

            printerStatus = STATUS_COOLING

        # Is waiting for cooling
        elif printerStatus is STATUS_COOLING:
            # Just finished cooling
            if time.time() - coolingStart >= COOLING_TIME:
                Serial.write(b"FAN OFF\n")
                Result = Serial.readline().decode('utf-8').rstrip()
                if Result == 'DONE':
                    log("Fan off")
                else:
                    log('Wrong result:' + Result)
                    raise Exception('Error trying to stop cooling')

                printerStatus = STATUS_EJECTING

        # Do ejection
        elif printerStatus is STATUS_EJECTING:
            Serial.write(b"LED ON\n")
            Result = Serial.readline().decode('utf-8').rstrip()
            if Result == 'DONE':
                log("Led on")
            else:
                raise Exception('Error trying to connect to ejector')

            # Ensure printer is in good position:
            postUrl('/api/printer/command', {'commands': ['G1 X125 Y210']})
            postUrl('/api/printer/command', {'commands': ['G1 Z210']})
            time.sleep(15)

            # Start ejection
            Serial.write(b"EJECT\n")
            Result = Serial.readline().decode('utf-8').rstrip()
            if Result == 'START':
                log("Ejection start")
            else:
                log('Wrong result:' + Result)
                raise Exception('Error trying to start ejection')

            # Wait for ejection to end
            Result = Serial.readline().decode('utf-8').rstrip()
            if Result == 'END':
                log("Ejection done")
            else:
                log('Wrong result:' + Result)
                raise Exception('Error waiting for ejection end')

            postUrl('/api/printer/command', {'commands': ['G1 Z10']})

            if AUTO_RESTART:
                printerStatus = STATUS_RESTARTING
            else:
                printerStatus = STATUS_IDLE

        # Restart print
        elif printerStatus is STATUS_RESTARTING:
            postUrl('/api/job', {'command': 'start'})
            log("Print restarted")
            printerStatus = STATUS_IDLE
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
